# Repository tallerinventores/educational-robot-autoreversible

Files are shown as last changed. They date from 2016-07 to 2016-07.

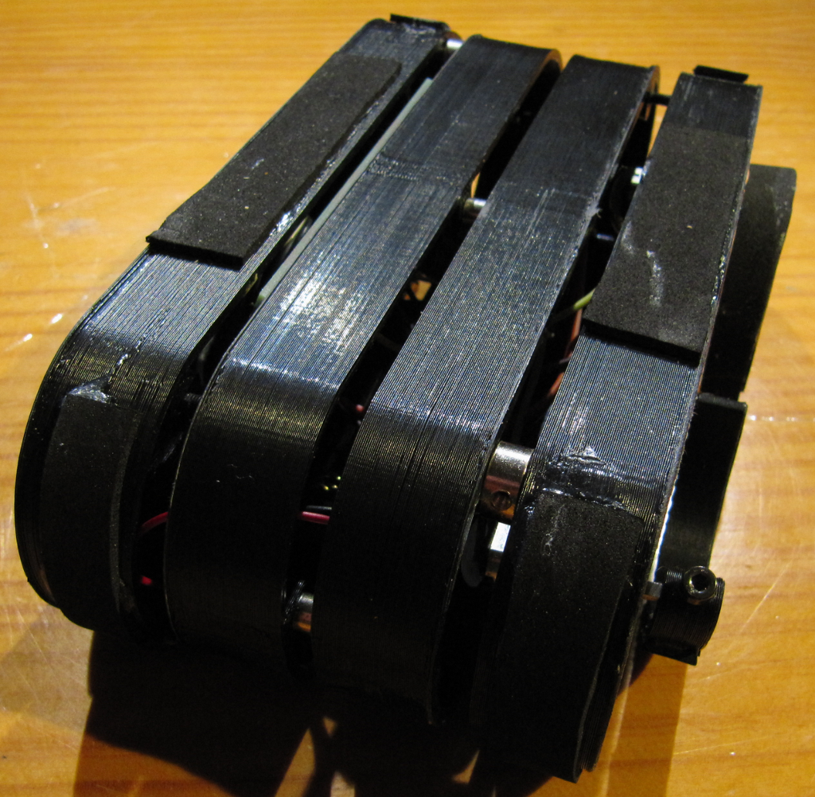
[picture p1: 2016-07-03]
img/photo-erar-2.png

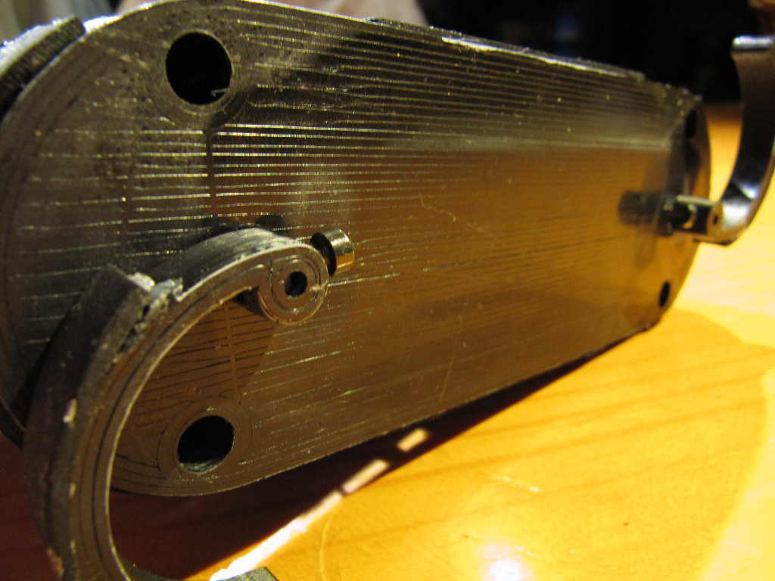
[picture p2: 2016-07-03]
img/photo-erar-7.png

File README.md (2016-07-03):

# educational-robot-autoreversible #

> RC robot autoreversible for educational use  

* * *

## Resumen ##

Robot radiocontrolado diseñado por los alumnos de la actividad de robótica
[Taller de Inventores](http://tallerinventores.github.io/). Ha sido desarrollado
y optimizado para impresión 3D y pensando en su bajo coste y facilidad de
montaje y uso.

## Instalación ##

En esta sección se cubre la instalación de software y hardware para el montaje
recomendado, mediante [Scratch](https://scratch.mit.edu/) y
[Arduino](http://www.arduino.cc/).

### Requerimientos de software ###

Para poder usar Scratch (v2.0 online) con Arduino, es necesario
[s2a_fm](https://github.com/MrYsLab/s2a_fm) una extensión de Scratch para
comunicarse con Arduino. Para generar los archivos aptos para la impresora 3D
desde los archivos `.stl` será necesario adicionalmente un software para esta
función, como puede ser [Slic3r](http://slic3r.org/).

### Requerimientos de hardware ###

Será necesario para su montaje y uso cuatro pilas tipo AA, cuatro motores con
reductora en miniatura, un sensor de proximidad por infrarrojos basado en
TCRT5000, una placa Robgednaut Zond con un Arduino Nano o compatible y un módulo
de bluetooth HC05. Adicionalmente hará falta tornillería variada de métrica
tres. Se recomienda un macho de misma métrica.  

## Uso ##

Instrucciones de montaje y puesta en marcha.

### Montaje del robot ###

1.  Imprimir una unidad de los archivos `internal.stl` e `internal-sensor.stl`.
    Imprimir dos unidades de `external-side.stl`. Imprimir cuatro unidades de 
    `leg.stl`. Puede ser necesario repasar las piezas impresas con el fin de
    eliminar rebabas.  
2.  Montar el sensor de proximidad en la pieza que permite su montaje
    (_internal-sensor_), fijándolo con un tornillo para plástico de diez
    milímetros de largo.  
3.  Fijar las dos partes interiores entre sí (_internal-sensor_ e _internal_),
    repasando los agujeros de una de las mitades para tres milímetros de
    diámetro, y hacer rosca en los correspondientes de la otra mitad. Atornillar
    ambas mitades con cuatro tornillos de métrica tres por veinticinco.  
4.  Colocar cada uno de los motores en las aperturas del chasis externo
    (_external-side_). Fijarlos en su posición con tornillos de cabeza hexagonal
    de métrica tres por veinte y una tuerca en el lado opuesto, o bien usando
    bridas.  
5.  Cerrar uno de los extremos del robot usando cuatro tornillos de métrica tres
    por treinta con una arandela, previa rosca en los agujeros de la mitad
    central.  
6.  Realizar todas las uniones eléctricas y meter todo el hardware necesario en
    el interior del chasis del robot.  
7.  Usar cuatro tornillos de métrica tres por treinta con arandela para cerrar
    el robot con la parte externa restante.  

### Conexión eléctrica ###

Este proyecto usa [Robgednaut](http://akornsys-rdi.github.io/robgednaut/) Zond
como placa de conexionado, si no dispones de ella puedes ver su esquema de
conexiones en la página oficial.  

Las alimentaciones para todos los dispositivos las provee la placa de control.
El cable de señal analógica del sensor de proximidad infrarrojo se conecta a A.
Los motores de cada lado van conectados en paralelo y a su vez a un canal de la
salida para motores, respetando su polaridad.

### Firmware ###

El Arduino deberá tener cargado el firmware Firmata (incluido con Arduino IDE
bajo en nombre de StandardFirmata).  

### Software ###

Con la comunicación bluetooth establecida (elementos emparejados), lanzar s2a_fm
con el nombre del puerto donde realizar la comunicación por bluetooth. Por
ejemplo:

        python s2a_fm.py /dev/rfcomm0

Abrir Scratch y cargar el proyecto educational-robot-autoreversible.sb2, una vez
hecho, se podrá ver en la interfaz gráfica los posibles movimientos del robot en
forma de flechas para dichas órdenes.

El robot avanzará en la dirección elegida hasta que sea detenido o cambiado de
dirección. El robot puede detenerse con el botón en forma de X. El botón
circular de paro de emergencia permite cancelar cualquier orden, deshabilitar el
robot y parar el programa. Después de pulsarlo será necesario volver a iniciar
el proyecto de Scratch.  

### Bugs ###

Se han observado los siguientes problemas:  

-   Debido a todo el hardware que va dentro del robot, ha sido necesario
    espaciar las partes para ganar espacio.  
-   El interruptor de encendido/apagado es difícil de accionar al quedar dentro
    de la estructura.  
-   El sotfware de control provoca al inicio movimientos extraños.  

## Enlaces externos ##

Este proyecto también está presente en:  

-   [Scratch](https://scratch.mit.edu/projects/112577118/).  
-   [Thingiverse](http://www.thingiverse.com/thing:1656800).  

## Créditos ##

Proyecto realizado por Taller de Inventores 2016, representado por:  

-   kwendenarmo <kwendenarmo@akornsys-rdi.net>  

Alumnos del Centro de Formación Padre Piquer:  

-   C, Duanju  
-   S, Saúl

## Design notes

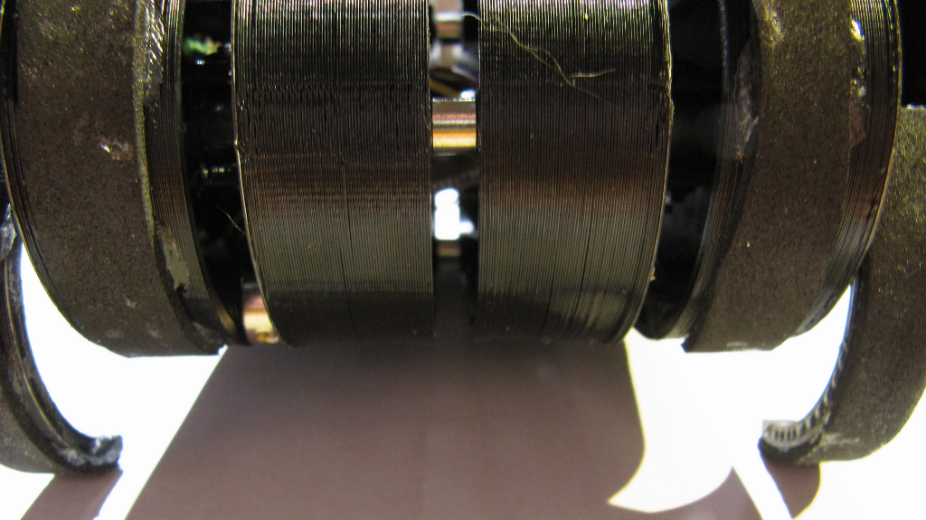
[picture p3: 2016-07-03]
img/photo-erar-8.png

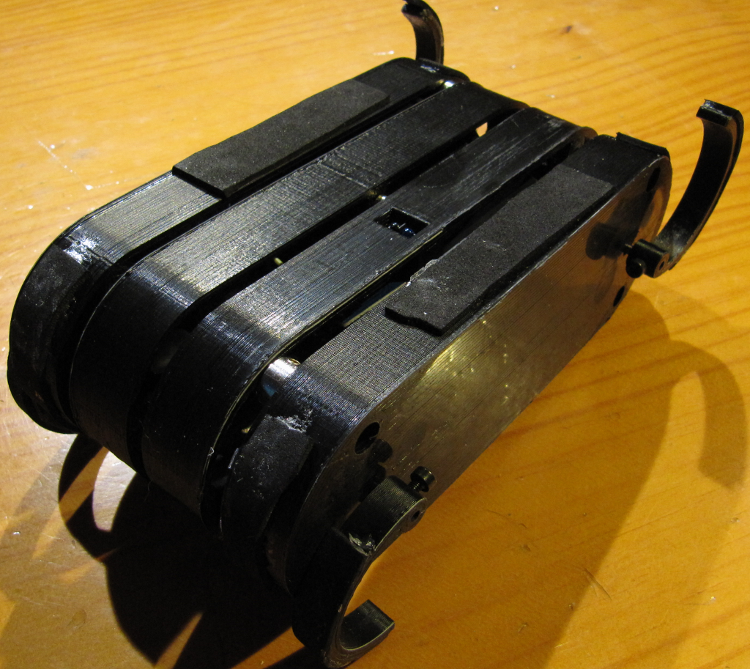
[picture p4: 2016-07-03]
img/photo-erar-5.png

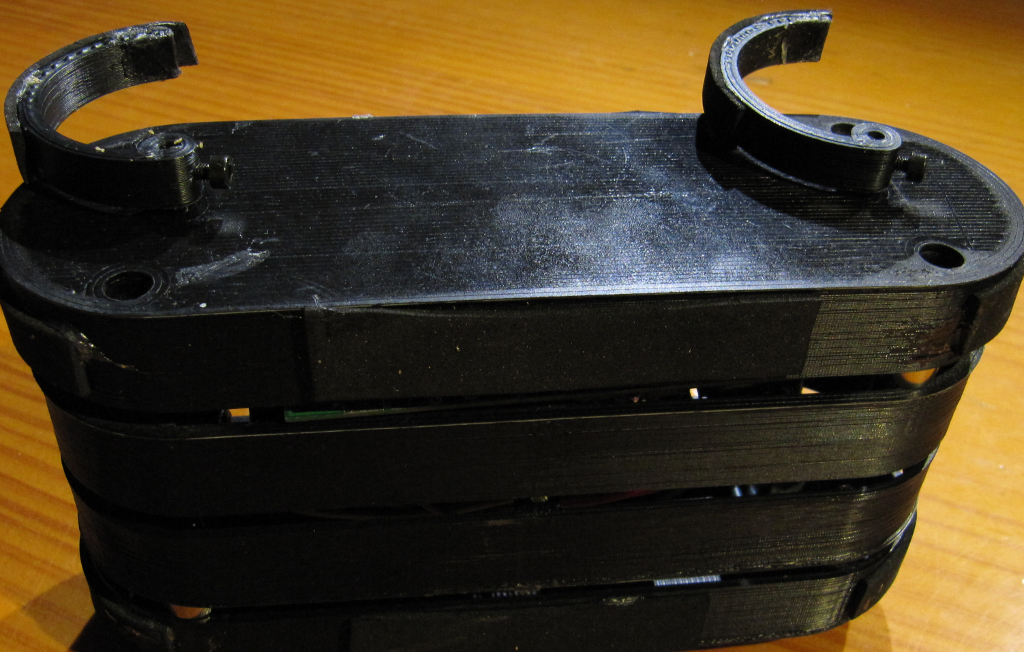
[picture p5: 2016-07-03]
img/photo-erar-4.png

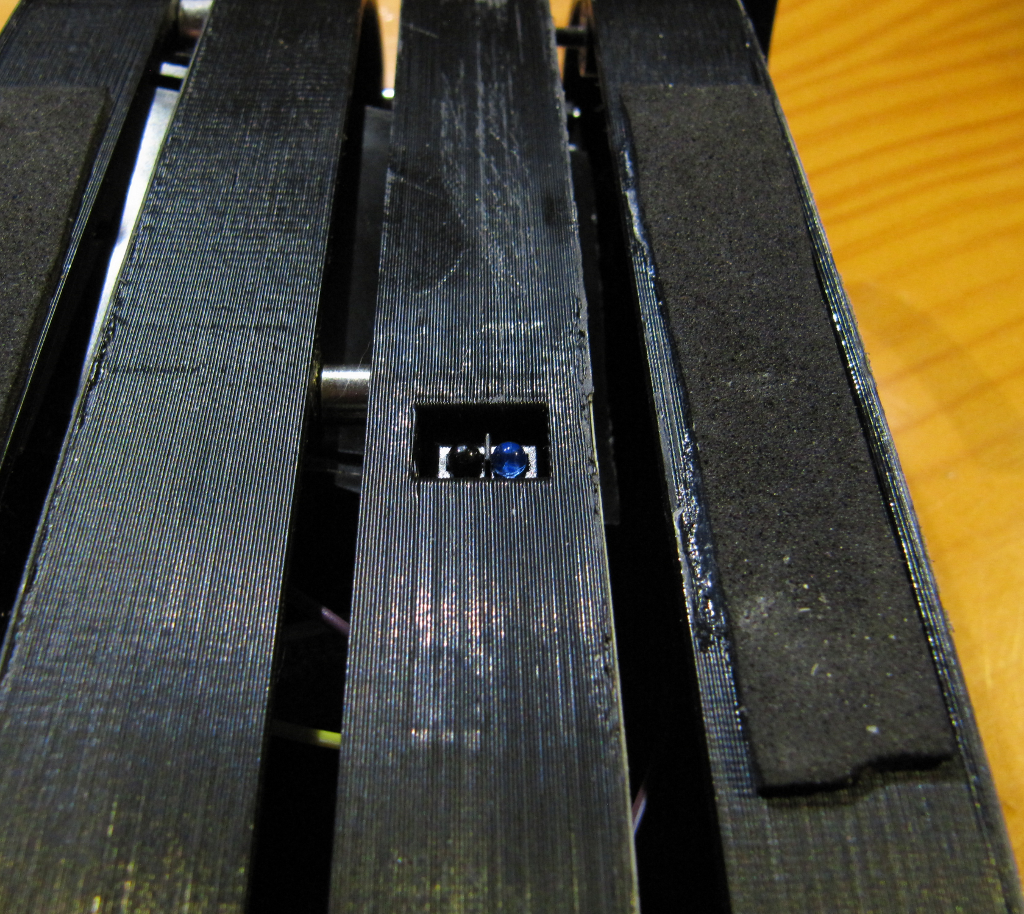
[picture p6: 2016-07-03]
img/photo-erar-6.png

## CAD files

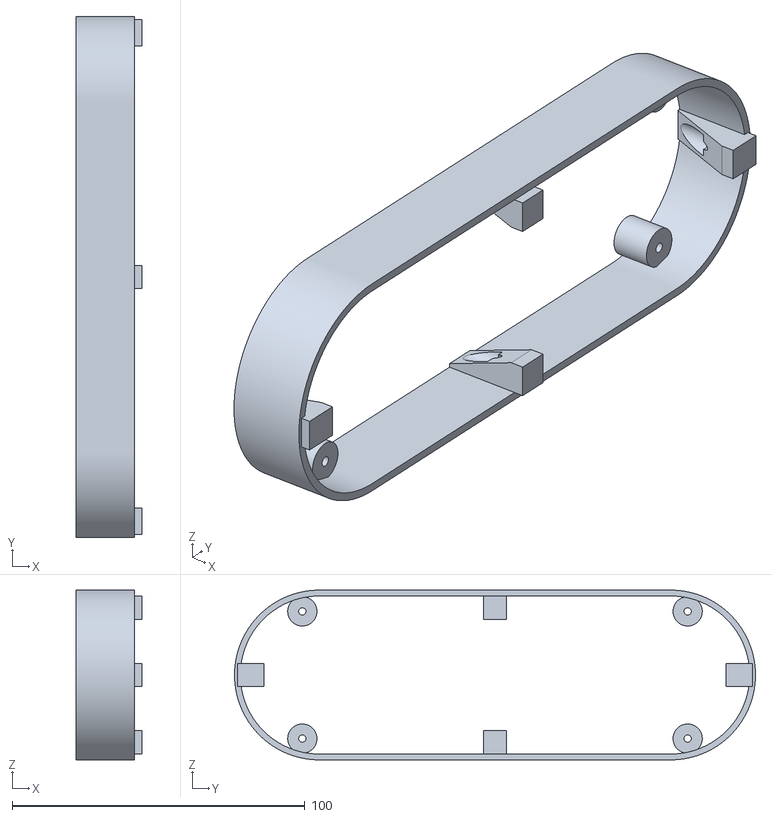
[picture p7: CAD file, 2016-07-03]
3d/internal.stl
22.5 x 178.0 x 58.0

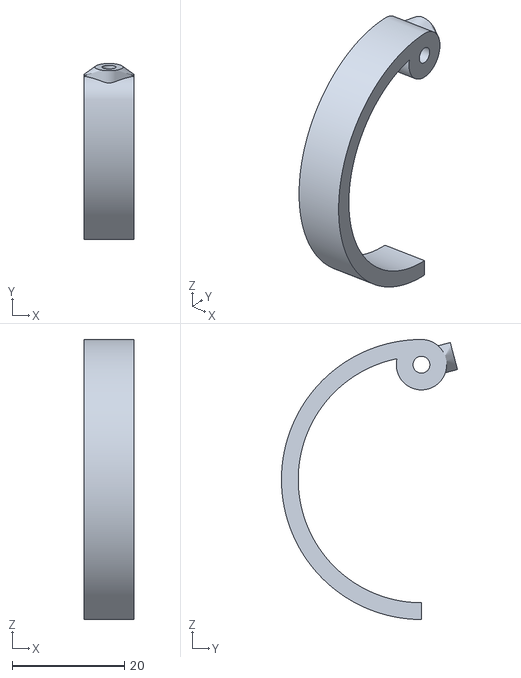
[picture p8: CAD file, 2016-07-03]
3d/leg.stl
9.00 x 31.4 x 50.0

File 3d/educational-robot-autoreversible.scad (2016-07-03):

/* {{{ %%SECTION_HEADER%%
 * * * *
 * This header information is automatically generated by KodeUtils.
 *
 * File 'educational-robot-autoreversible.scad' edited by kwendenarmo,
 * last modified: 2016-07-03.
 * This file is part of 'educational-robot-autoreversible' package, please see
 * the readme files for more information about this file and this package.
 *
 * Copyright (C) 2016 by kwendenarmo <kwendenarmo@akornsys-rdi.net>
 * Released under the GNU GPLv3
 *
 *    This program is free software: you can redistribute it and/or modify
 *    it under the terms of the GNU General Public License as published by
 *    the Free Software Foundation, either version 3 of the License, or
 *    (at your option) any later version.
 *
 *    This program is distributed in the hope that it will be useful,
 *    but WITHOUT ANY WARRANTY; without even the implied warranty of
 *    MERCHANTABILITY or FITNESS FOR A PARTICULAR PURPOSE.  See the
 *    GNU General Public License for more details.
 *
 *    You should have received a copy of the GNU General Public License
 *    along with this program.  If not, see <http://www.gnu.org/licenses/>.
 *
 * * * *
 * %%EOS_HEADER%% }}}
 */

$fn=360;

/*
 *  Tornillos
 *  -   Sensor 1x 3x10 plastico
 *  -   Motor 4x M3x20 hex
 *  -   Cierre chasis 8x M3x30 + 1 arandela plana
 *  -   Cierre chasis interior 4x M3x25
 */

chasis_lateral();
translate([-25.5,0,0]) chasis_central(1);
translate([-30.5,0,0]) mirror() chasis_central();
translate([-56,0,0]) mirror() chasis_lateral();
translate([30,-60,29]) rotate([0,-90,0]) pala();
translate([30,60,29]) rotate([0,-90,0]) pala();
translate([-77,-60,29]) rotate([0,-90,0]) pala();
translate([-77,60,29]) rotate([0,-90,0]) pala();

module chasis_lateral() {
    difference() {
        //chasis
        union() {
            hull() {
                translate([0, -60, 29]) rotate([270, 270, 270]) cylinder(r=29, h=20);
                translate([0, 60, 29]) rotate([270, 0, 270]) cylinder(r=29, h=20);
            }
            translate([-5.5,60,29]) rotate([75,0,0]) translate([0,22.5,0]) rotate([0,90,0]) cylinder(r=5, h=5.5);
            translate([-5.5,60,29]) rotate([-75,0,0]) translate([0,22.5,0]) rotate([0,90,0]) cylinder(r=5, h=5.5);
            translate([-5.5,-60,29]) rotate([105,0,0]) translate([0,22.5,0]) rotate([0,90,0]) cylinder(r=5, h=5.5);
            translate([-5.5,-60,29]) rotate([-105,0,0]) translate([0,22.5,0]) rotate([0,90,0]) cylinder(r=5, h=5.5);
        }
        union() {
            //chasis interior
            difference() {
                hull() {
                    translate([-1, -60, 29]) rotate([270, 270, 270]) cylinder(r=27, h=19);
                    translate([-1, 60, 29]) rotate([270, 0, 270]) cylinder(r=27, h=19);
                }
                //soportes motor delantero
                difference() {
                    union() {
                        translate([19,-71.5,21.5]) hull() {
                            cube([1,23,2]);
                            translate([-19,0,1]) cube([1,23,2]);
                        }
                        translate([19,-71.5,34.5]) hull() {
                            cube([1,23,2]);
                            translate([-19,0,-1]) cube([1,23,2]);
                        }
                    }
                    union() {
                        translate([5,-69,20.5]) cylinder(r=1.75, h=17);
                        translate([5,-51,20.5]) cylinder(r=1.75, h=17);
                    }
                }
                //soportes motor trasero
                difference() {
                    union() {
                        translate([19,48.5,21.5]) hull() {
                            cube([1,23,2]);
                            translate([-19,0,1]) cube([1,23,2]);
                        }
                        translate([19,48.5,34.5]) hull() {
                            cube([1,23,2]);
                            translate([-19,0,-1]) cube([1,23,2]);
                        }
                    }
                    union() {
                        translate([5,51,20.5]) cylinder(r=1.75, h=17);
                        translate([5,69,20.5]) cylinder(r=1.75, h=17);
                    }
                }
                //taladros de montaje
                union() {
                    translate([-2,60,29]) rotate([75,0,0]) translate([0,22.5,0]) rotate([0,90,0]) cylinder(r=5, h=22);
                    translate([-2,60,29]) rotate([-75,0,0]) translate([0,22.5,0]) rotate([0,90,0]) cylinder(r=5, h=22);
                    translate([-2,-60,29]) rotate([105,0,0]) translate([0,22.5,0]) rotate([0,90,0]) cylinder(r=5, h=22);
                    translate([-2,-60,29]) rotate([-105,0,0]) translate([0,22.5,0]) rotate([0,90,0]) cylinder(r=5, h=22);
                }
            }
            //motores
            union() {
                translate([17, -60, 29]) rotate([0,90,0]) cylinder(r=2.25, h=4);     //motor delantero
                translate([17, -66.5, 23.5]) cube([2, 13, 11]);     //rebaje motor delantero
                translate([17, 60, 29]) rotate([0,90,0]) cylinder(r=2.25, h=4);      //motor trasero
                translate([17, 53.5, 23.5]) cube([2, 13, 11]);      //rebaje motor trasero
            }
            //agujero de montaje
            union() {
                translate([5,60,29]) rotate([75,0,0]) translate([0,22.5,0]) rotate([0,90,0]) cylinder(r=3.75, h=16);
                translate([5,60,29]) rotate([-75,0,0]) translate([0,22.5,0]) rotate([0,90,0]) cylinder(r=3.75, h=16);
                translate([5,-60,29]) rotate([105,0,0]) translate([0,22.5,0]) rotate([0,90,0]) cylinder(r=3.75, h=16);
                translate([5,-60,29]) rotate([-105,0,0]) translate([0,22.5,0]) rotate([0,90,0]) cylinder(r=3.75, h=16);
                translate([-6,60,29]) rotate([75,0,0]) translate([0,22.5,0]) rotate([0,90,0]) cylinder(r=1.25, h=13);
                translate([-6,60,29]) rotate([-75,0,0]) translate([0,22.5,0]) rotate([0,90,0]) cylinder(r=1.25, h=13);
                translate([-6,-60,29]) rotate([105,0,0]) translate([0,22.5,0]) rotate([0,90,0]) cylinder(r=1.25, h=13);
                translate([-6,-60,29]) rotate([-105,0,0]) translate([0,22.5,0]) rotate([0,90,0]) cylinder(r=1.25, h=13);
            }
        }
    }
}
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
